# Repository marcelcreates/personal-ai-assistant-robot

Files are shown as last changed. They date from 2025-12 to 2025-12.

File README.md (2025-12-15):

# personal-ai-assistant-robot
This is a personal AI assistant robot. Powered by OpenAI's Realtime API and having the ability to integrate with smart home devices, it can have a conversation in real time, answer questions, perform tasks and move around, all whilst being able to display information and animations on its front facing oled, and control its build in addressable led lights. This inital version (v1) is a basic MVP to test how everything will come together, but future versions will include temperature, light intensity and touch sensors, a camera and an auto charging dock. As this project doesn't require any custom PCB's I have not included any PCB files.

I began this project mainly because I was getting frustrated with my alexa not being able to understand anything more complex than 'set a timer', and now with how advanced LLM's are getting I thought It would be a nice opportunity to create my own version of a home assistant who could actually hold a conversaion but also do everything the alexa could (appart from 'speaker' aspect). All whilst having the enjoyment that comes from working on a project like this.

## The Body (Empty)
topSideView
sideBottomView
frontBottomView

With this inital design (v1):
- the Raspberry Pi screws into the top (the mouting holes can be seen in the image above)
- the oled slides into two channels behind the opening on the front side
- the speaker sticks behind the grill (double sided tape comes pre applied with the speaker)
- the usb mic sits flush in the circular opening on the fronts side
- the n20 motors are inserted into the two rear wheels to spin the rubber tracks

## Wiring Diagram
Bellow is a wiring diagram to represent how all the components (listed in the BOM) will be wired, I have not included the 7.4v 18650 battery connection to the XL4015 as the wiring there is self explanatory, also the digital to analog converter on the right represents the PCM2704 part as I could not find the part visual anywhere on the internet
WiringDiagram

## BOM
The BOM is available here in the docs folder: [View BOM](docs/BOM%20-%20v1.csv)

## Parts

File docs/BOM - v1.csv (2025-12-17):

GRANT Items | Description | Quantity | Unit Price | Total Price | Item Link
Raspberry pi 4 B |  | 1 | $57.00 | $57.00 | https://thepihut.com/products/raspberry-pi-4-model-b?variant=20064052674622
Raspberry Pi 4 cooling fan | Cooling fan | 1 | $4.00 | $4.00 | Raspberry Pi 5 Active Cooler Aluminum Heatsink PWM Speed Adjustable Fan Black Silver Blue Cooling Radiator for RPI 5 Pi5 - AliExpress 7
PLA Fillament | Body | 1 | $24.00 | $24.00 | https://uk.store.bambulab.com/products/pla-matte?id=40215560978492
ESP32 | Controller for audio and motors | 1 | $4.00 | $4.00 | ESP32 WROOM-32 Development Board TYPE-C Micro USB WiFi+Bluetooth Ultra-Low Power Consumption SPI Flash 32Mbits Wireless Module - AliExpress
SSD1322 3.2 inch oled | Oled display | 1 | $16.00 | $16.00 | DIYTZT Real OLED Display 3.12" 256*64 25664 Dots Graphic LCD Module Display Screen LCM Screen SSD1322 Controller Support SPI - AliExpress
WS2812B strip lights | Addressable LED lights | 1 | $4.00 | $4.00 | https://www.aliexpress.com/item/2036819167.html
7.4V 8000mah Li-ion | Battery | 1 | $8.00 | $8.00 | https://www.aliexpress.com/item/1005010315311296.html
XL4015 | buck step down module | 1 | $1.50 | $1.50 | 1-10pcs XL4015 Constant Voltage Current Step Down Buck Module DC-DC 5V-32V to 0.8V-30V 5A adjust Lithium Battery Charger Board - AliExpress
N20 150RPM motors | Movment | 2 | $8.00 | $16.00 | GA12-N20 DC 3V 6V 12V Micro Metal Gear Motor Gear Wheel Gear Motor 30RPM 50RPM 60RPM 100RPM 150RPM 200RPM 300RPM 600RPM 1000RPM - AliExpress 13
USB Mic | Audio input | 1 | $2.00 | $2.00 | https://www.aliexpress.com/item/1005006032566949.html
TB6612FNG | Motor dirver | 1 | $1.50 | $1.50 | TB6612 DRV8833 Dual Motor Driver 1A TB6612FNG for Arduino Microcontroller Better than L298N - AliExpress
4ohm 3W speaker | Audio output | 1 | $2.00 | $2.00 | 2PCS 3525/2535 Speaker 4Ohm 3W 4Ohm 2W Full Range BOX Cavity Sound Speaker High Fidelity Speaker Accessories - AliExpress
XT30 connectors | Battery to buck connectors | 1 | $1.70 | $1.70 | XT30 XT-30 Plug Male Female Bullet Connectors Plugs For RC Lipo Battery Quadcopter Multicopter For Aircraft accessories parts - AliExpress
PAM8403 | Audio amplifer | 1 | $1.30 | $1.30 | Mini PAM8403 DC 5V 2 Channel USB Digital Audio Amplifier Board Module 2 * 3W Volume Control with Potentionmeter - AliExpress
PCM2704 | digital to analog convertor | 1 | $2.00 | $2.00 | https://www.aliexpress.com/item/1005010419248796.html?curPageLogUid=Cx0zuczwZokt
SELF PROVIDED ITEMS (NO GRANT REQUIRED)
330ohm resistor
64GB SDcard
4 M2.5 screws
N-Channel MOSFET
 |  | TOTAL FOR GRANT ITEMS: |  | $145.00

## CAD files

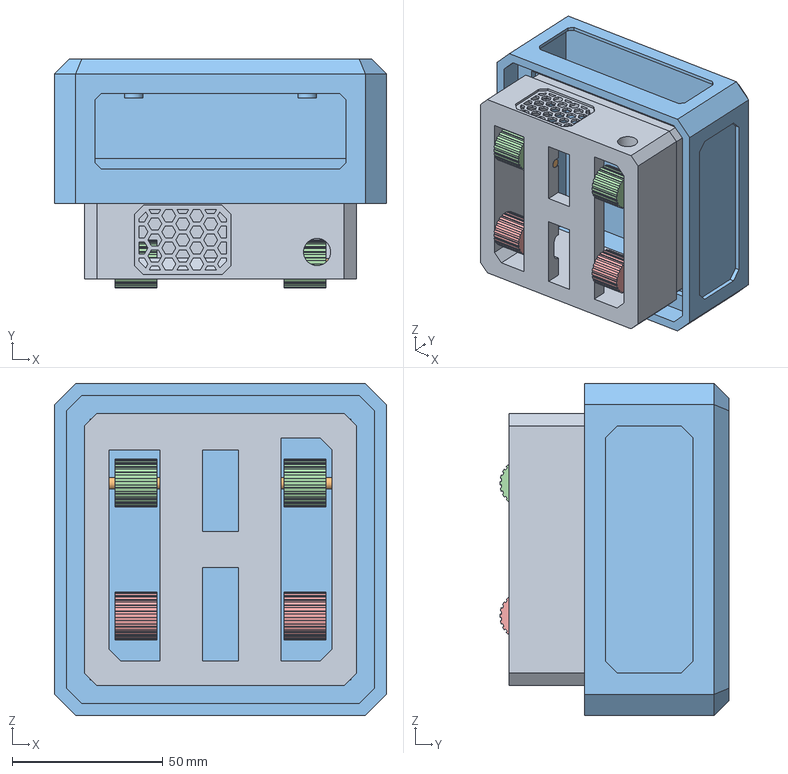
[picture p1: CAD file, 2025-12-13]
CAD/ai-assistant-body.step
110.0 x 76.0 x 110.0 mm

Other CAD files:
CAD/body.f3d

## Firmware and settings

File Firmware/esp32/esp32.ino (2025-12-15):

#include <FastLED.h>

#define LED_PIN 15
#define NUM_LEDS 16

#define AIN1 26
#define AIN2 25
#define BIN1 33
#define BIN2 32
#define STBY 27

CRGB leds[NUM_LEDS];

void setup() {
  Serial.begin(115200);

  pinMode(AIN1, OUTPUT);
  pinMode(AIN2, OUTPUT);
  pinMode(BIN1, OUTPUT);
  pinMode(BIN2, OUTPUT);
  pinMode(STBY, OUTPUT);
  digitalWrite(STBY, HIGH);

  FastLED.addLeds<WS2812B, LED_PIN, GRB>(leds, NUM_LEDS);
  FastLED.clear();
  FastLED.show();
}

void stopMotors() {
  digitalWrite(AIN1, LOW);
  digitalWrite(AIN2, LOW);
  digitalWrite(BIN1, LOW);
  digitalWrite(BIN2, LOW);
}

void moveForward() {
  digitalWrite(AIN1, HIGH);
  digitalWrite(AIN2, LOW);
  digitalWrite(BIN1, HIGH);
  digitalWrite(BIN2, LOW);
}

void turnLeft() {
  digitalWrite(AIN1, LOW);
  digitalWrite(AIN2, HIGH);
  digitalWrite(BIN1, HIGH);
  digitalWrite(BIN2, LOW);
}

void loop() {
  if (Serial.available()) {
    String cmd = Serial.readStringUntil('\n');
    cmd.trim();

    if (cmd == "MOVE_FORWARD") moveForward();
    else if (cmd == "TURN_LEFT") turnLeft();
    else if (cmd == "STOP") stopMotors();
    else if (cmd == "LIGHTS_TOGGLE") {
      fill_solid(leds, NUM_LEDS, CRGB::Blue);
      FastLED.show();
    }
  }
}

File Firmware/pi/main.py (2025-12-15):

import asyncio
import serial
import speech_recognition as sr
from realtime_audio import RealtimeAudioClient
from luma.core.interface.serial import spi
from luma.oled.device import ssd1322
from PIL import Image, ImageDraw

WAKE_WORD = "cypher"
SERIAL_PORT = "/dev/ttyUSB0"
BAUD = 115200

oled_serial = spi(device=0, port=0)
oled = ssd1322(oled_serial)

def oled_show(text):
    img = Image.new("RGB", oled.size)
    draw = ImageDraw.Draw(img)
    draw.text((10, 10), text, fill="white")
    oled.display(img)

esp = serial.Serial(SERIAL_PORT, BAUD, timeout=1)

def send_cmd(cmd):
    esp.write((cmd + "\n").encode())
  
def handle_intent(text):
    t = text.lower()
    if "forward" in t:
        send_cmd("MOVE_FORWARD")
    elif "left" in t:
        send_cmd("TURN_LEFT")
    elif "stop" in t:
        send_cmd("STOP")
    elif "lights" in t:
        send_cmd("LIGHTS_TOGGLE")

r = sr.Recognizer()
mic = sr.Microphone()

def wait_for_wake():
    with mic as source:
        r.adjust_for_ambient_noise(source)

    while True:
        with mic as source:
            audio = r.listen(source)
        try:
            if WAKE_WORD in r.recognize_google(audio).lower():
                return
        except:
            pass

async def main():
    oled_show("Cypher online")

    while True:
        wait_for_wake()
        oled_show("Listening...")

        client = RealtimeAudioClient()
        await client.run()

        oled_show("Ready")

if __name__ == "__main__":
    asyncio.run(main())

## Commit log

2025-12-13 Created CAD Folder
2025-12-13 Added Initial CAD File (v1)
    [ai-assistant-body.step]
2025-12-15 Added screenshots of the body and the wiring diagram
2025-12-15 added BOM to docs
    [BOM - v1.csv]
2025-12-15 Added BOM to README
2025-12-15 Added the main.py code for raspberry pi
2025-12-15 Added firmware for esp32
2025-12-15 Added source design file
    [body.f3d]
2025-12-17 Updated BOM
    [BOM - v1.csv]
